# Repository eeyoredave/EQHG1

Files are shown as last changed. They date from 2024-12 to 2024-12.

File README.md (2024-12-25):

# EQHG1 Equatorial mount with harmonic gearing project
<h1>Introduction</h1>

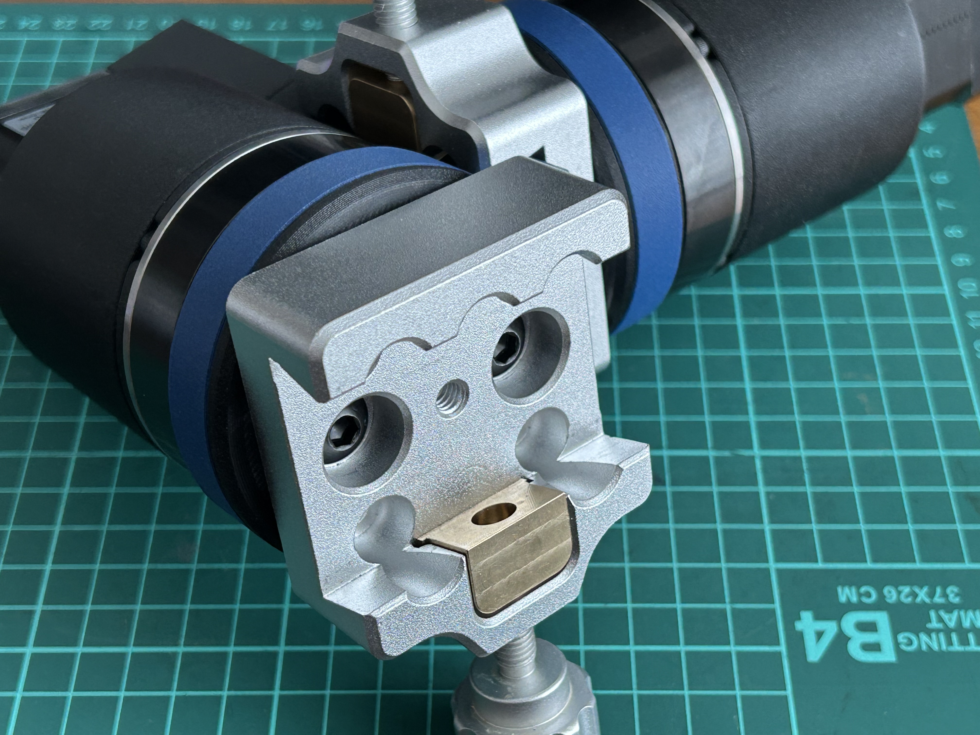
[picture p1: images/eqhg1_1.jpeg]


<p>This is my record of a DIY equatorial mount for astronomy use. It is a design based on various collated ideas from other projects and and it is designed to be built easily using readily available parts and 3D printed parts. Whilst the goal has not been to make this the cheapest project, consideration has been made in terms of 'value for money'. Please note, none of the links are affiliates, etc., they are just links to the products that I purchased myself and used on this project. It was designed to be clamped with the Vixen Dovetail standard. I only have a few clamps on hand, but they all seem to work fine.</p>

<p>It is set up in a modular fashion that building only one of the two motors, it can be used as a simple sky tracker. Using two will allow it to be used as a GoTo mount with dual axis tracking - each module is identical. You could even cascade 4 mounts to create an auto-PA Goto EQ mount! All 3D printed parts were printed on my Bambu P1S using Bambu Labs PETG-CF. I am sure other printer and filament combinations can be used, but you may need to test fit the parts as required. </p>

<p>As built, each module weights 1.537 g, so a total weight of just over 3.0 kg.</p>

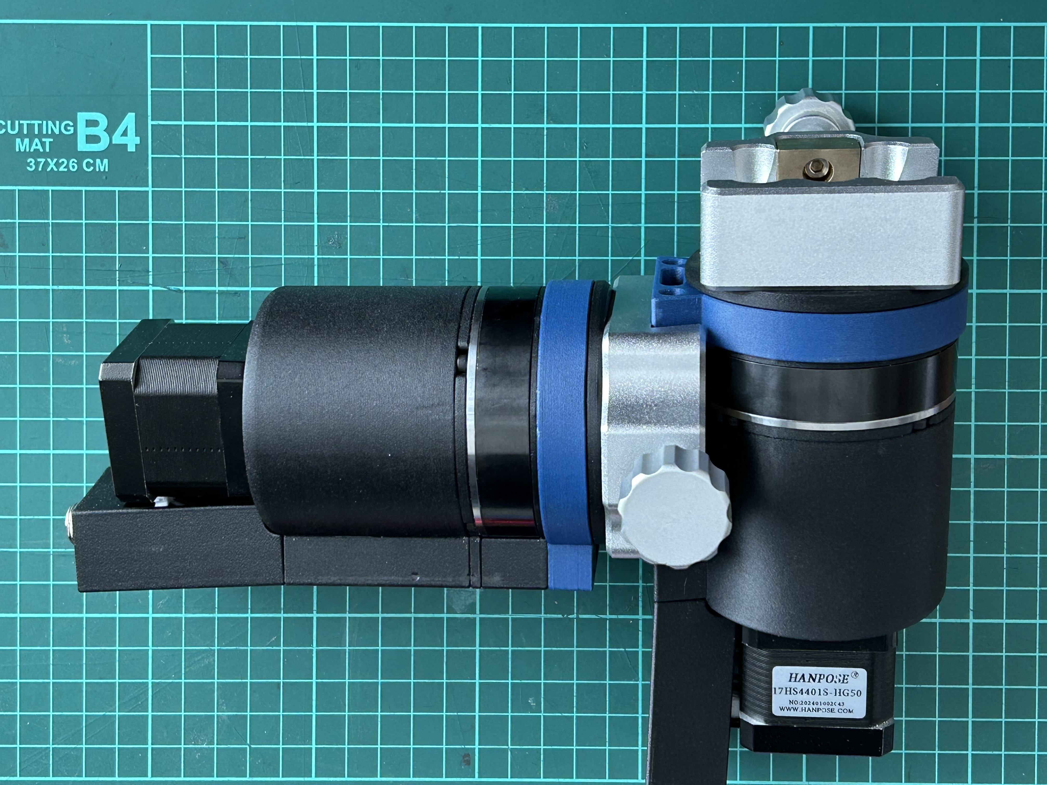
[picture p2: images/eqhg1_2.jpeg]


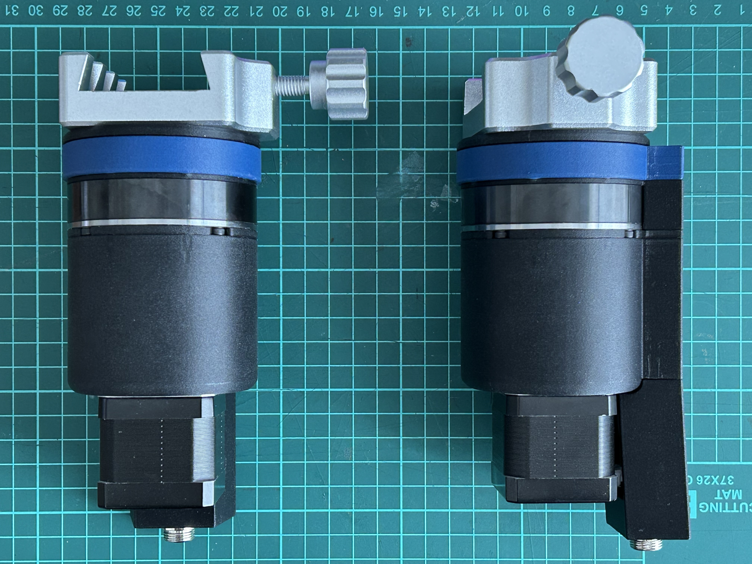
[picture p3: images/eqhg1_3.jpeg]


<h1>BoM</h1>
<p>The below is for 1 motor, you will need 2 for a full GoTo/2 axis tracking mount. You can substitute different parts or motos gear ratios to match your needs, but I will not be able to provide additional STL files, etc..</p>
<h2>Hardware</h2>
<ul>
<li>1x ZXF14 100:1 Harmonic Gear (https://www.aliexpress.com/item/1005006514715087.html)</li>
<li>1x 50:1 Nema 17 Planetry Gear (https://www.aliexpress.com/item/1005007382016476.html)</li>
<li>1x 6810ZZ Bearing</li>
<li>1x Universal Dovetail plate ('Style Two' https://www.aliexpress.com/item/1005002630127603.html)</li>
<li>1x Yellow grease (but I used red lithium, as that is what I had on hand)</li>
<li>M3 SHCS</li>
<li>M4 SHCS</li>
<li>M8 SHCS</li>
<li>M3 Heat inserts (RutheX size 4.6 mm diameter 5.7 mm length)</li>
</ul>

<h2>3D Printed Parts</h2> 

<p>All the of the modelling was done in Rhino 3D v8. Yes, it is not a true parametric modeller like Fusion, etc., but it is a package that I own, have been using for over 20 years and thus familiar with it. There are a total of 6 printed parts, all were prototyped in PETG-HF (https://store.bambulab.com/products/petg-hf) and final printed in PETG-CF (https://store.bambulab.com/products/petg-cf). I used the CF product because I liked the colours and finish better, does not specifically require drying before use (though I have a drying cabinet) and the mechanical properties are slightly better. Of course, feel free to use whatever you desire or have on hand.</p>
<p>It has been designed to be printed without any supports and also split to allow some colour creativity on your part. I had no issues printing any of the parts in my Bmabu P1S and the settings I used were basically a strong 0.20 mm.</p>
<ol>
  <li>EQ_PG_Body_04 Main Body (to connect the NEMA17 motor)</li>
  <li>EQ_PG_Spacer_01 Sepacer Ring (to clear the ZXF14 body screw heads)</li>
  <li>EQ_HG_Spacer_01 Harmonic Gear Separator (to space the ZXF14 from the main body but maintain the dovetail rail)</li>
  <li>EQ_HG_Body_03 Harmonic Gear mounting ring (to mount the sandwhich the harmonic gear to the main body and also enclose the 6810 bearing)</li>
  <li>EQ_Output_Plate_03 Output Plate (to connect the harmonic gear to the dovetail clamp plate and also sits within the 6810 bearing)</li>
  <li>EQ_MotorConnect_03 GX12 socket mount (to connect the NEMA17 motor to the GX12 cable) This is the one part I am not happy with, it doesn't sit right, and the connection between the motor and the socket is not ideal, I would like to improve this.</li>
</ol>

<h2>Electronic</h2>
<p>I have used a Fystec E4 as the OnStepX controller board and found that the settings that works well so far to be (for both motors):</p>
<ul>
<li>Steps per degree: 44,444.444</li>
<li>Microsteps: 16</li>
<li>Everything as standard as per the OnStepX fresh install</li>
</ul>

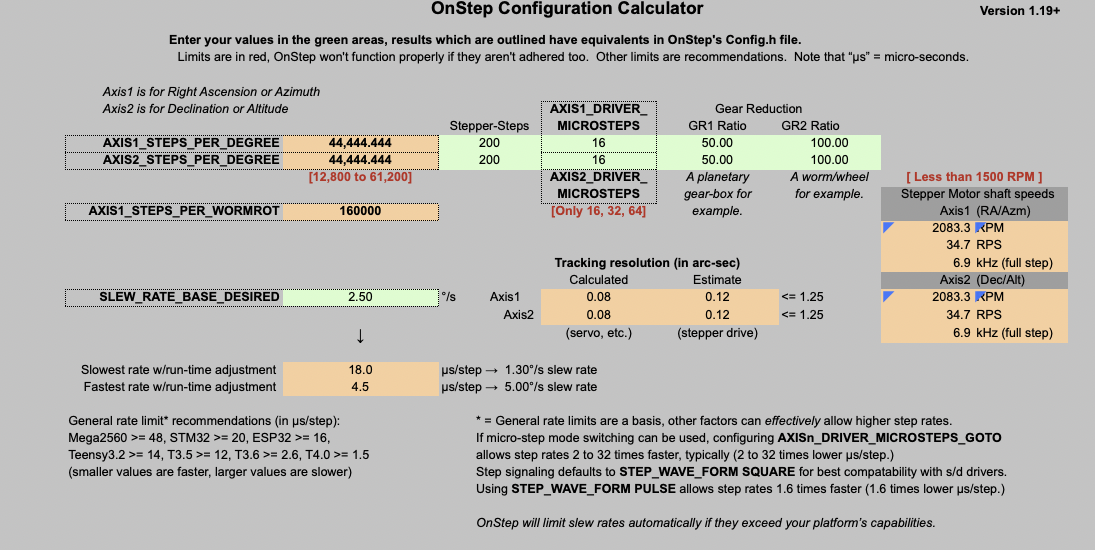
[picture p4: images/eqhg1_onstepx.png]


<p>For reference, I tried reducing the microsteps to 8 or lower, to increase slewing speed, but found it to slip and stall. It would appear that a minimum of 16 microsteps works well so far.</p>

<h1>Testing</h1>
<p>My current load is an Askar SQA55/ASI622MC with EAF and a 30mm guidescope/ASI120MM - quite a light load. Having used this with an OnStepX controller and AsiAir Lite, I have found that the tracking erros have been in the region of 1.0 RMS typically, reaching as low as 0.64 RMS. So far, I've had no issues with up to 2 minute exposures using auto-guiding. This was done from my Bortle 9 high rise balcony, with only a rough eyeball PA (I did not use the PA function as yet).</p>

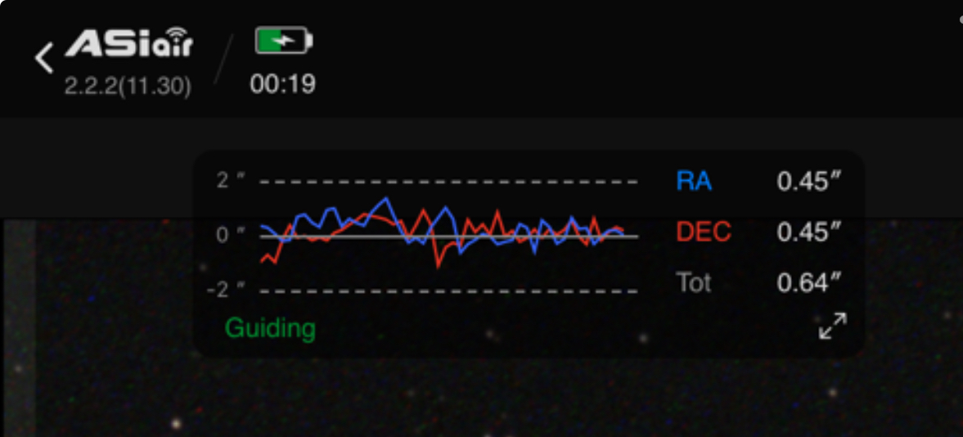
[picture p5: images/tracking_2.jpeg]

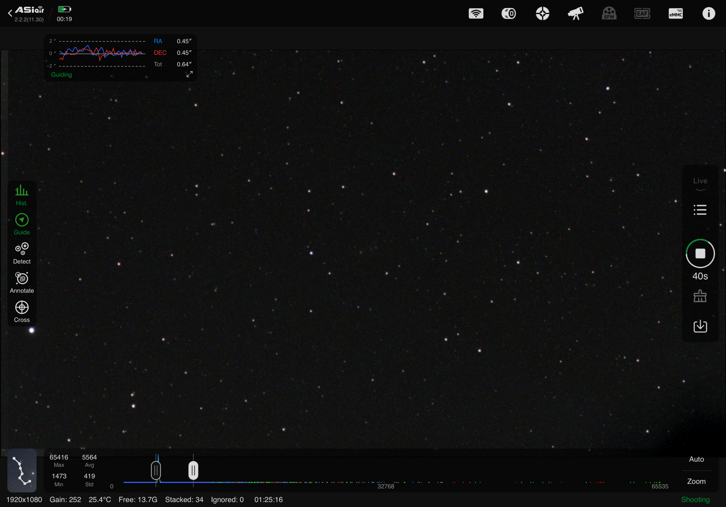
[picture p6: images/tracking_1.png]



<p>Here are some initial images taken with the mount, using the Askar SQA55 with ASI662MC camera with autoguiding on a 30mm/ASI120MM scope. Please note that I have only being doing astrophotography for a month, as I started in Nov 2024. The image was capture using this mount, processed in PixInsight with various proceses (GraXpert, BlurXT, NoiseXT and StarXT), I am <u>NOT an experienced AP</u>. I am learning and still have a <i>long, long, long</i> way to go.</p>

<figure>
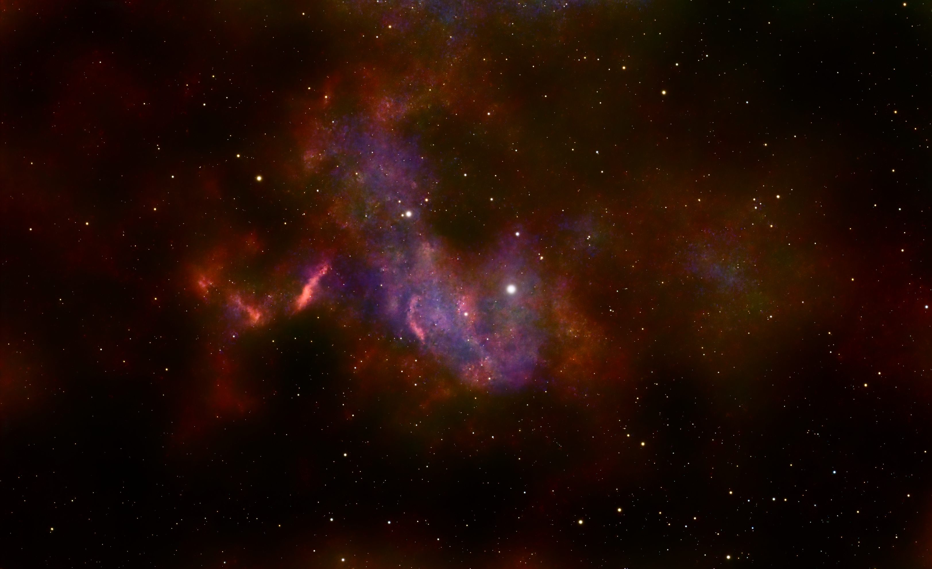
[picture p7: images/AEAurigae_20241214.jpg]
    
    <figcaption>AE Aurigae taken Dec 2024. 125x 30 second subs. There are some star trailing, direction of the trails are from the top left to bottoh right, maybe due to poor PA, but to be further reviewed and tweaked.</figcaption>
</figure>

<h1>Next Steps</h1>
<p>More testing is required. In more conditions, under different loads, tracking times, etc. I will for sure try it with my Takahashi FC-100DC, though its fairly light, it is quite a long tube which might start to test its true performance.</p>
<p>Moving forward, I would like to consider if using a 27:1 PG gear as a more appropriate first stage, as that could still provide a similar steps per degree, 48,000 using 32 microsteps but also an option for lower steps at 24,000 steps using 16 microsteps. Or even using a 50:1 harmonic gear.</p>

<p>As the next 'evolution' of the project, I would like to consider having a 'single body' mount, where both the DEC and RA are on one body with the electronics. In this arrangement, I would try to reduce the weight and bulk and make it a portable travel GoTo EQ mount. Targeting a 2 kg limit or so and including all the components within the single body, so only need to add power. Mount connection could be done with Wi-Fi or USB.</p>

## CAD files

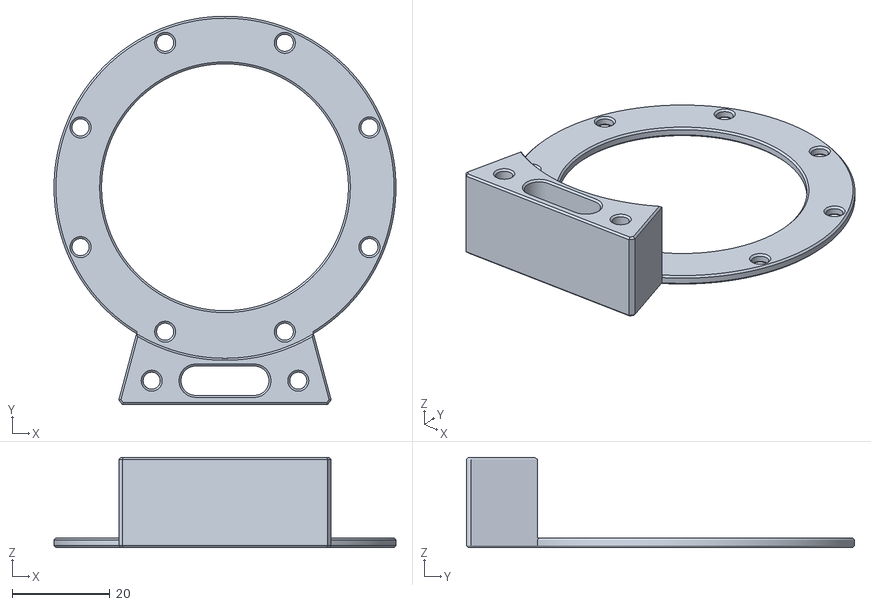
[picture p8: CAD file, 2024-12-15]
STL/EQ_HG_Spacer_01.stl
70.0 x 79.5 x 18.5

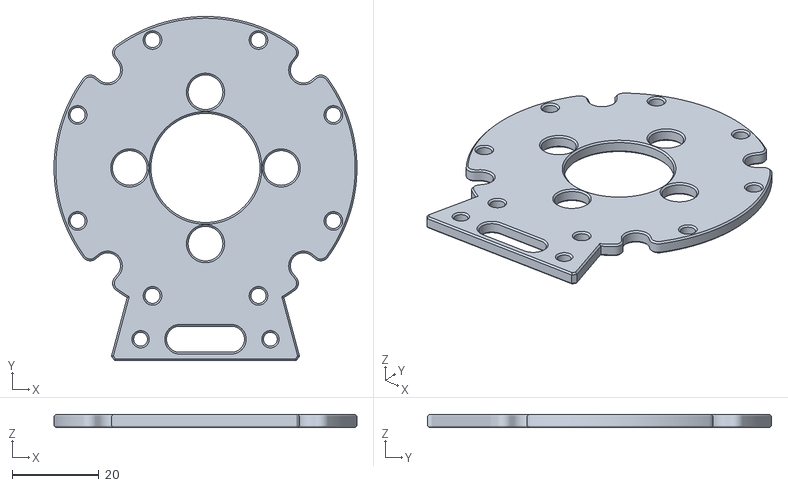
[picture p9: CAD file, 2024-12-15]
STL/EQ_PG_Spacer_01.stl
70.0 x 79.5 x 3.00

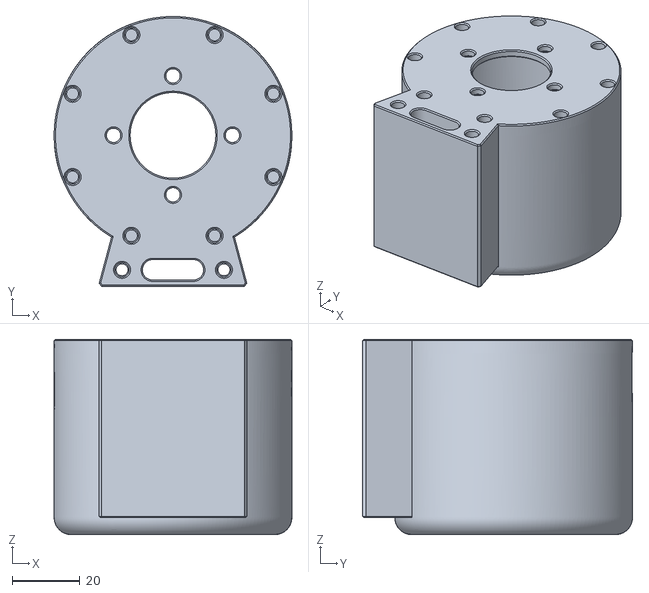
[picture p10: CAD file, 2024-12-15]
STL/EQ_PG_Body_04.stl
70.0 x 79.5 x 57.5

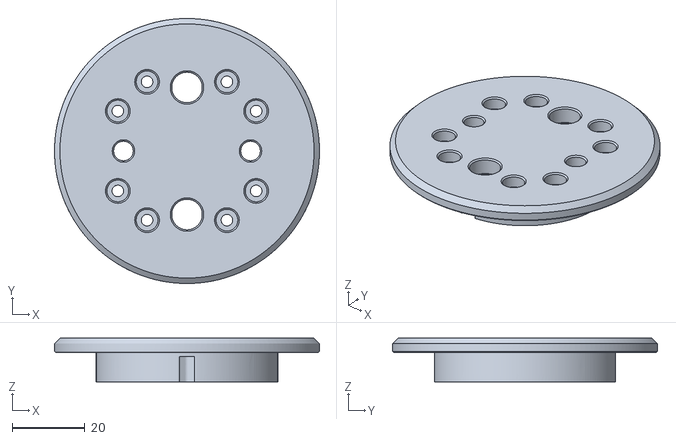
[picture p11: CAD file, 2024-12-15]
STL/EQ_Output_Plate_03.stl
73.0 x 73.0 x 12.0

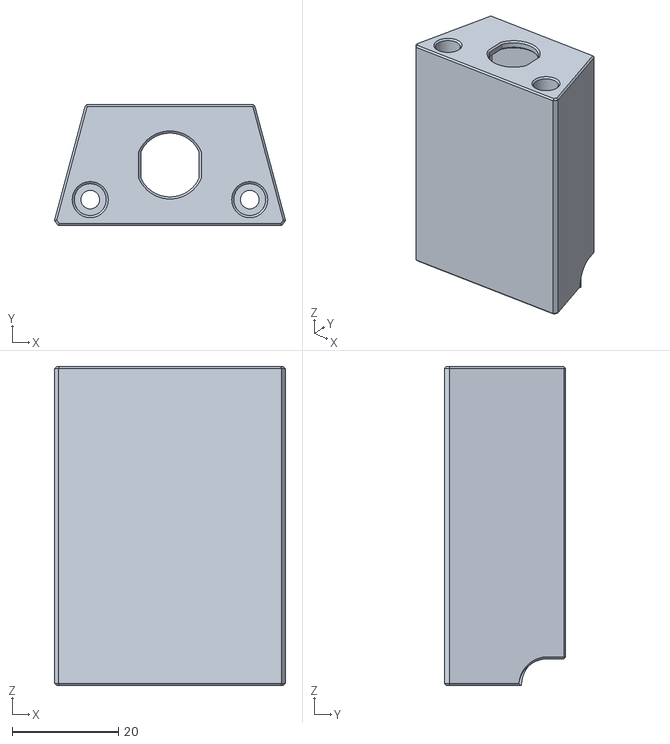
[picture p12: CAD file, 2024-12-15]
STL/EQ_MotorConnect_03.stl
43.5 x 22.9 x 60.0

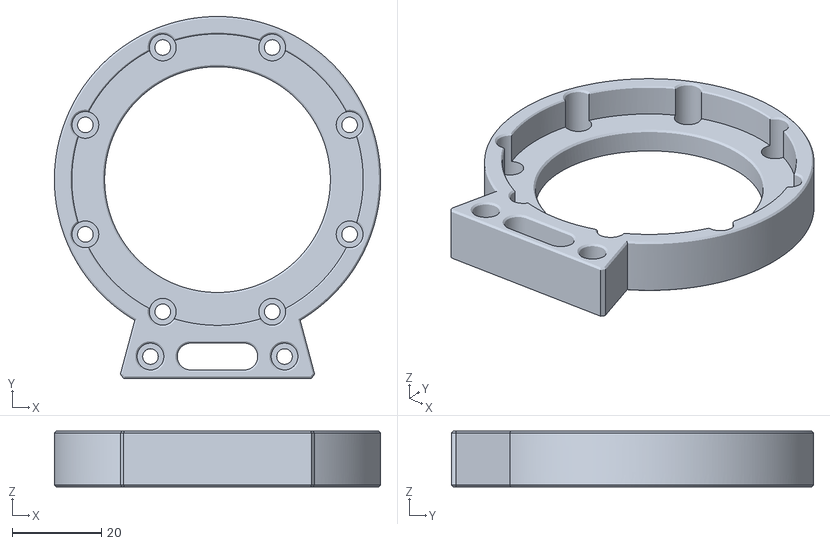
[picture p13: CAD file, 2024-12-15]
STL/EQ_HG_Body_03.stl
73.0 x 81.0 x 12.5
